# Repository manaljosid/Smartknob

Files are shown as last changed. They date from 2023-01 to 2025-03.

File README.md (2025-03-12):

# Smartknob
A smartknob clone based on the [original project](https://github.com/scottbez1/smartknob) from Scott Bezek.

A couple changes are implemented including:
- Change of microcontroller from ESP32 to RP2040
- Change of load cell setup from dedicated loadcells to resistors
- Change of HX711 load cell amplifier to MCP3564R 24-bit ADC
- Change of RGB LEDs to ones from Adafruit

The project uses Altium Designer for schematic and PCB design, Autodesk Fusion 360 for mechanical design and the Pico SDK for software development.

## Heads-up!
No guarantee is made that anything in this repository will work. Currently all changes are committed directly to the main branch and as such the main branch can contain bugs or have changes that have yet to be completed.

## Installation
### Schematic and PCB design
The designs are made with the latest version of Altium Designer and as such the software along with a valid license is required.

In addition to Altium Designer the component library used for all of my projects needs to be installed. It can be found on this [github repository](https://github.com/manaljosid/Moonlight_Library).

### Mechanical design
The mechanical design is not available at the moment other than the STL files used for 3D printing.

### Software development
In addition to pulling this repository you need to fetch all required submodules. Those include the actual pico-sdk and its submodules. Make sure the submodules are all installed, if the submodules of the pico-sdk are not installed then no USB function other than the boot ROM will work.

Due to issues in the release of the pico-sdk being used for this code (mainly that the clock configuration is hard coded) a development branch is used.

## Things to watch out for
The MCP3564R *NEEDS* a pull-up on the IRQ line when it is in high-z mode. It can be weak - about 100 kOhm will do but if it is not there the ADCDATA register will never contain any data. In this case it is solved using a pull-up on the RP2040s GPIO pin that's connected to the IRQ line.

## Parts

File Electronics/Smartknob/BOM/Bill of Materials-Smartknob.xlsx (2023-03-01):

Description | Supplier | Designator | Supplier Part No | Quantity | Fitted | Generic | Value
General purpose ceramic capacitor | Digi-Key | C100 | 445-5691-1-ND | 1 | Fitted | Generic | 2.2uF
General purpose ceramic capacitor | Digi-Key | C101, C208, C209, C504, C505 | 445-174215-1-ND | 5 | Fitted | Generic | 1uF
General purpose ceramic capacitor | Digi-Key | C102, C302, C303 | 445-16110-1-ND | 3 | Fitted | Generic | 10uF
General purpose ceramic capacitor | Digi-Key | C200, C201, C202, C203, C204, C205, C206, C207, C210, C211, C300, C301, C304, C305, C400, C500, C501, C502, C503, C600, C601, C602, C603, C604, C605, C606, C607, C608 | 445-5666-1-ND | 28 | Fitted | Generic | 100nF
General purpose ceramic capacitor | Digi-Key | C212, C213 | 445-5634-1-ND | 2 | Fitted | Generic | 33pF
Side mounted RGB neopixel | Digi-Key | D600, D601, D602, D603, D604, D605, D606, D607 | 1528-4691-ND | 8 | Fitted | Non Generic | RGB
PTC resettable SMD fuse | Digi-Key | F200 | MF-PSMF050X-2CT-ND | 1 | Fitted | Generic | 500 mA
Ferrite bead | Digi-Key | FB500 | 587-FBTH1608HL221-TCT-ND | 1 | Fitted | Generic
3 pin horizontal picoblade connector | Digi-Key | J100 | WM7621CT-ND | 1 | Fitted | Non Generic
2mm pitch solder pads, M1.6 Hole, Unplated, M2 Hole, Unplated, SMD Testpoint, pad style |  | J101, M100, M101, M102, M103, M104, M105, M106, M107, M108, TP200 |  | 11 | Fitted | Generic
3 pin vertical 2.54 mm header | Digi-Key | J102 | 732-5316-ND | 1 | Fitted | Generic
USB 2.0 Type C connector | Digi-Key | J200 | 670-DX07S016JA1R1500CT-ND | 1 | Fitted | Non Generic
General purpose automotive thick film resistor | Digi-Key | R100, R101 | 541-2.2KGCT-ND | 2 | Not Fitted | Generic | 2K2
General purpose automotive thick film resistor | Digi-Key | R200, R205 | 541-1.0KGCT-ND | 2 | Fitted | Generic | 1K
General purpose automotive thick film resistor | Digi-Key | R201, R204 | 541-5.10KHCT-ND | 2 | Fitted | Generic | 5K1
General purpose automotive thick film resistor | Digi-Key | R202, R203 | 541-27GCT-ND | 2 | Fitted | Generic | 27R
General purpose automotive thick film resistor | Digi-Key | R206, R300, R301, R302, R303, R304, R305 | 541-10KGCT-ND | 7 | Fitted | Generic | 10K
General purpose automotive thick film resistor | Digi-Key | R400, R401 | 541-2.2KGCT-ND | 2 | Fitted | Generic | 2K2
General purpose automotive thick film resistor | Digi-Key | R500, R501 | 541-10GCT-ND | 2 | Fitted | Generic | 10R
General purpose automotive thick film resistor | Digi-Key | R502, R503, R506, R507 | 541-330XCT-ND | 4 | Fitted | Generic | 330R
General purpose automotive thick film resistor | Digi-Key | R504, R505 | 541-100GCT-ND | 2 | Fitted | Generic | 100R
General purpose automotive thick film resistor | Digi-Key | R508 | 541-0.0GCT-ND | 1 | Fitted | Generic | 0R
SPST Tactile Switch 4.2x3.2 mm | Digi-Key | SW200, SW201 | 732-13663-1-ND | 2 | Fitted | Non Generic
SMD Testpoint, loop style | Digi-Key | TP100, TP101, TP102, TP103, TP201, TP202 | 36-5019CT-ND | 6 | Fitted | Generic
3.3V 700mA LDO linear regulator | Digi-Key | U100 | 893-1143-1-ND | 1 | Fitted | Non Generic
128 Mbit SPI/QSPI Flash memory | Digi-Key | U200 | W25Q128JVSIQ-ND | 1 | Fitted | Non Generic
Dual Core 133 MHz ARM-M0 Microcontroller | Digi-Key | U201 | 2648-SC0908(7)CT-ND | 1 | Fitted | Non Generic
2-11V 2A 3-phase BLDC motor driver | Digi-Key | U300 | 1460-TMC6300-LA-TCT-ND | 1 | Fitted | Non Generic
Hall effect absolute magnetic encoder | LCSC | U400 | C2856764 | 1 | Fitted | Non Generic
Low-noise 24-bit Delta-Sigma ADC, 2/4/8 ch single ended, 1/2/4 ch differential | Digi-Key | U500 | 150-MCP3564RT-E/STCT-ND | 1 | Fitted | Non Generic
Single Buffer CMOS Level Shifter | Digi-Key | U600 | 296-37176-1-ND | 1 | Fitted | Generic
12 MHz 10ppm crystal oscillator | Digi-Key | X200 | XC1810CT-ND | 1 | Fitted | Non Generic | 12 MHz

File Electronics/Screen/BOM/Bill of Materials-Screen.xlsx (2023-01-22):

Description | Supplier | Designator | Supplier Part No | Quantity | Fitted | Generic | Value
General purpose ceramic capacitor | Digi-Key | C1 | 445-5666-1-ND | 1 | Fitted | Generic | 100nF
General purpose ceramic capacitor | Digi-Key | C2, C3 | 445-16110-1-ND | 2 | Fitted | Generic | 10uF
2mm pitch solder pads, M1.6 Hole, Unplated |  | J1, J2, M1 |  | 3 | Fitted | Generic
General purpose N-Channel MOSFET in SOT23 packagge | Digi-Key | Q1 | BSS138CT-ND | 1 | Fitted | Generic | NMOS
General purpose automotive thick film resistor | Digi-Key | R1 | 541-22GCT-ND | 1 | Fitted | Generic | 22R
General purpose automotive thick film resistor | Digi-Key | R2 | 541-10KGCT-ND | 1 | Fitted | Generic | 10K
General purpose automotive thick film resistor | Digi-Key | R3 | 541-1.0MGCT-ND | 1 | Fitted | Generic | 1M
240x240 px round IPS display | N/A | U1 | N/A | 1 | Fitted | Non Generic | Display

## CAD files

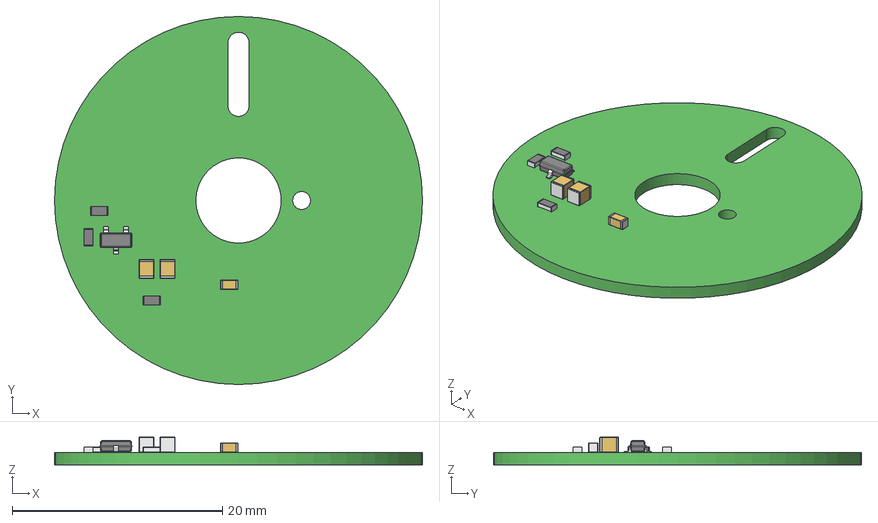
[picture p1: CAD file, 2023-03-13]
Electronics/Screen/Screen.step
35.0 x 35.0 x 2.65 mm
Mid_Body x 3
Mark x 3
Leader x 3

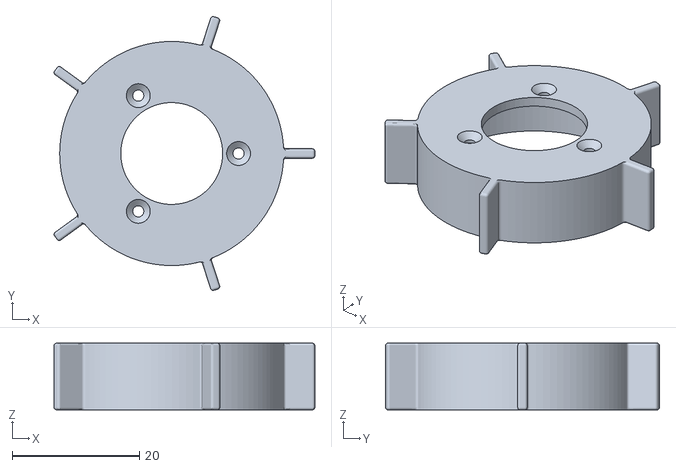
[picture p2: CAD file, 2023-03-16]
Mechanical/Exports/RotorSpacer.stl
41.0 x 43.0 x 10.5

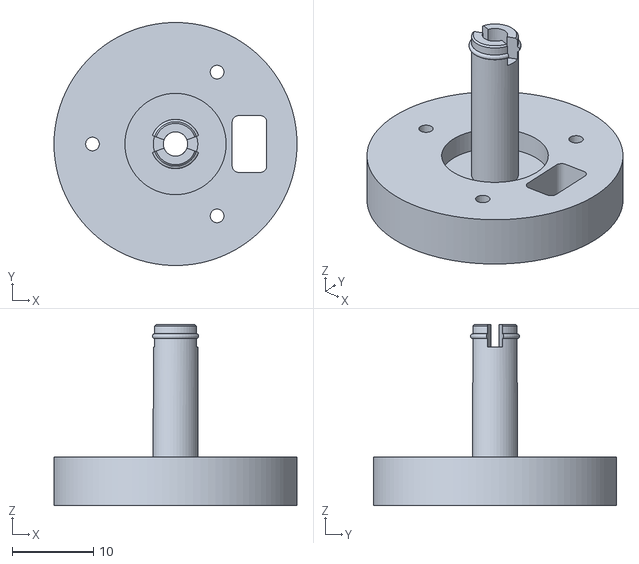
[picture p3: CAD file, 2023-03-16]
Mechanical/Exports/BaseMount.stl
30.0 x 30.0 x 22.3

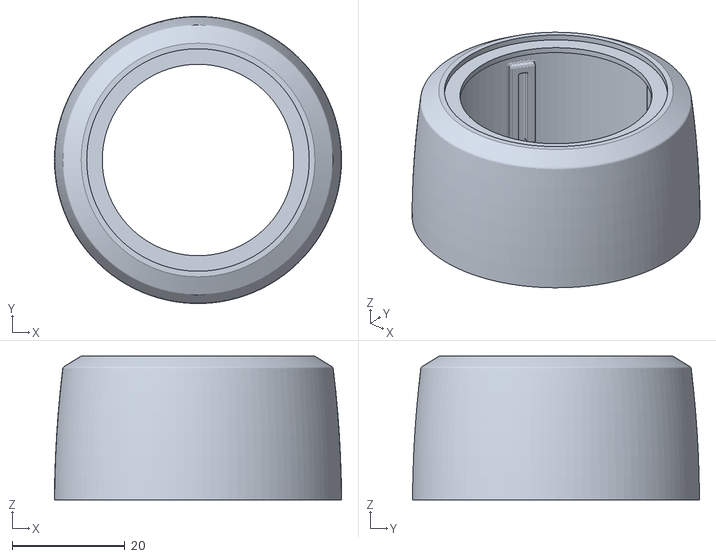
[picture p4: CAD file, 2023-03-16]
Mechanical/Exports/Knob.stl
51.0 x 51.0 x 25.6

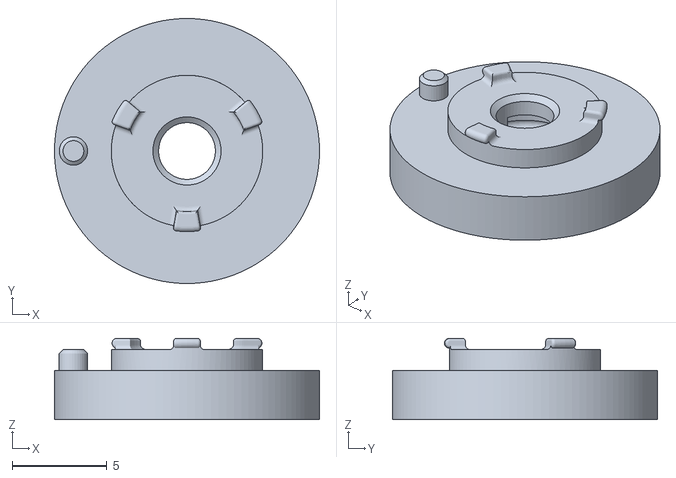
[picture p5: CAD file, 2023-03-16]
Mechanical/Exports/ScreenPlatform.stl
14.0 x 14.0 x 4.30

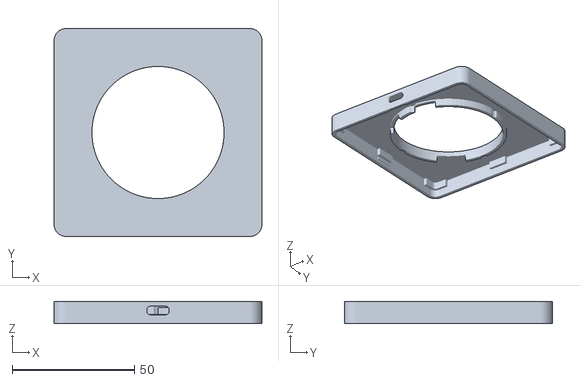
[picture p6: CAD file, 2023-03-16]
Mechanical/Exports/Enclosure.stl
85.0 x 85.0 x 9.00

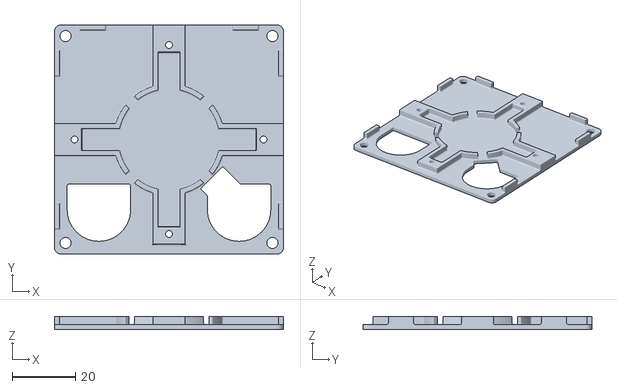
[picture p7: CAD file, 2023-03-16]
Mechanical/Exports/Baseplate.stl
72.2 x 72.2 x 4.00

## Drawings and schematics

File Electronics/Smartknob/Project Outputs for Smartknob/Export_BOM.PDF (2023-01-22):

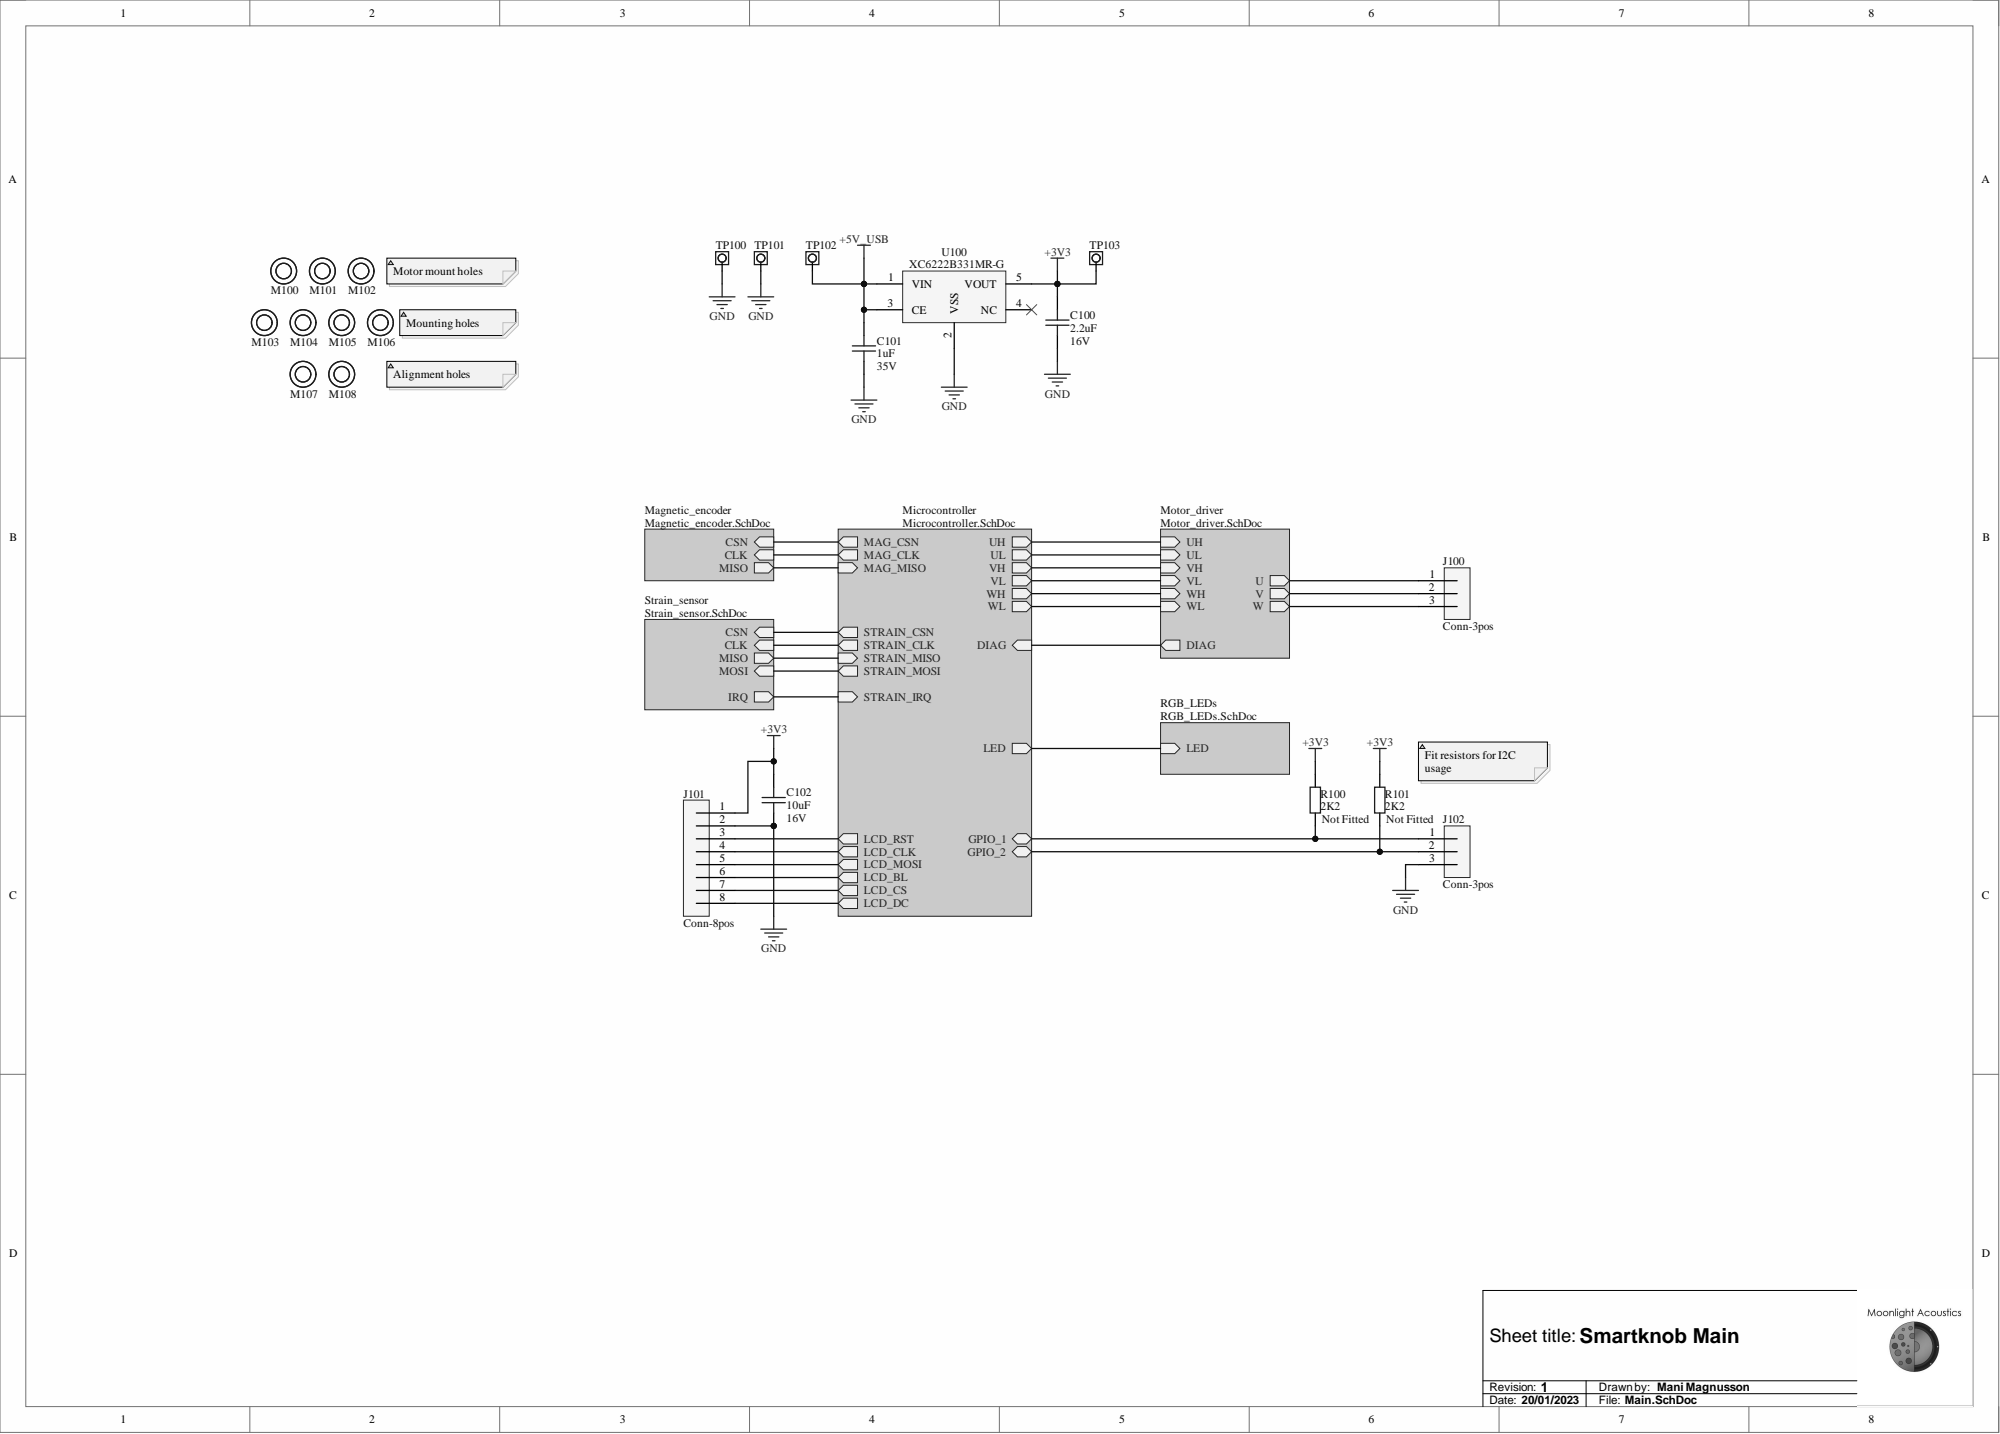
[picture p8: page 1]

Drawn by: Mani Magnusson
File: Main.SchDoc

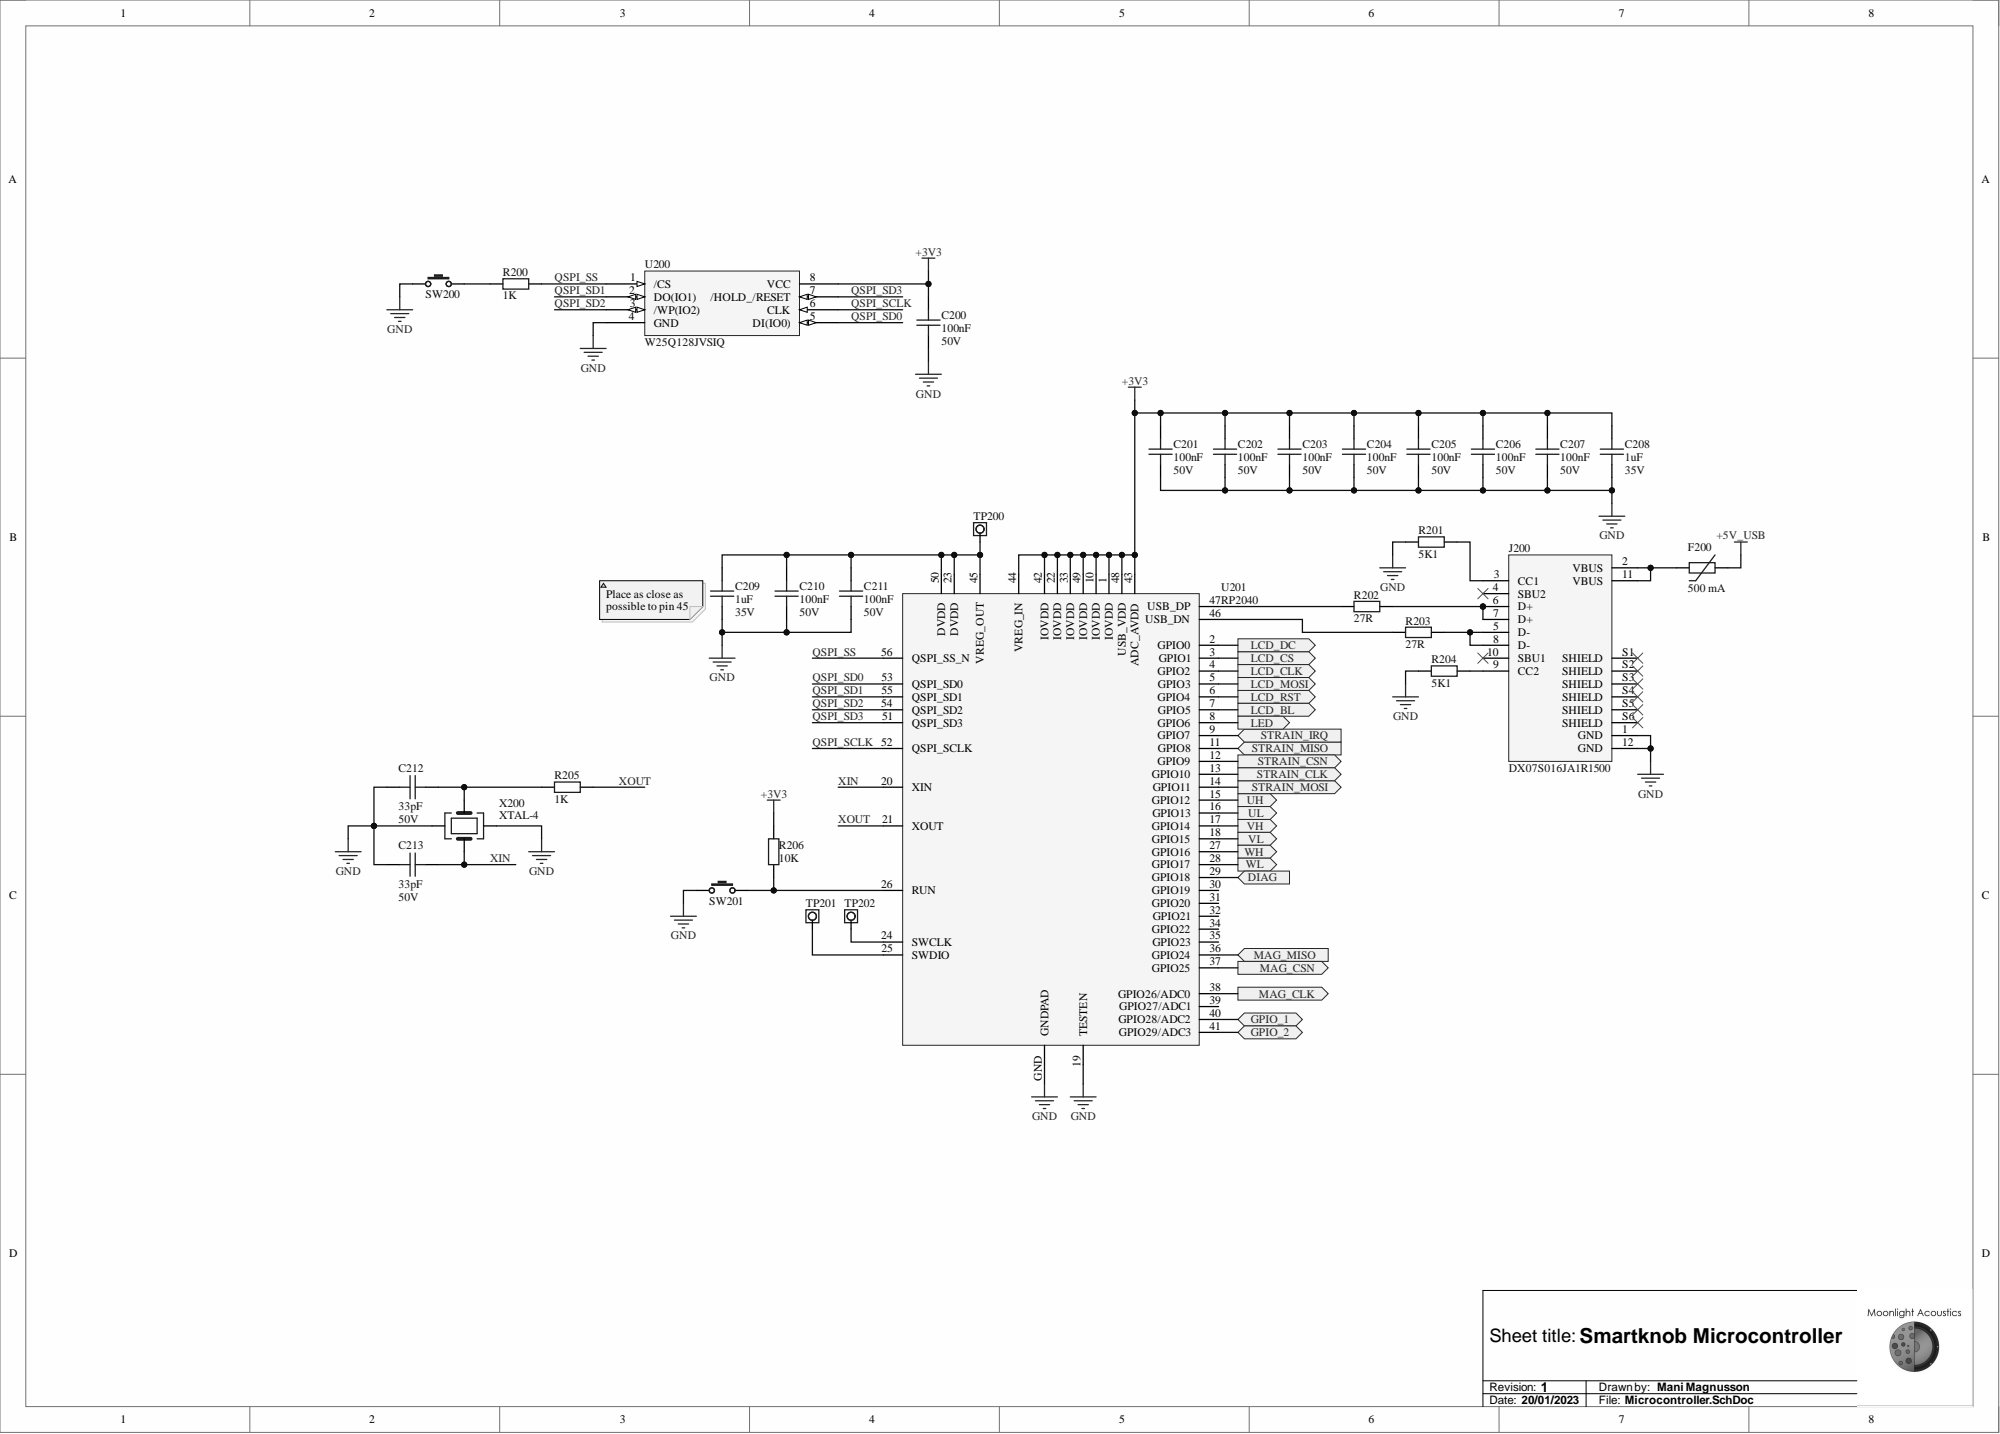
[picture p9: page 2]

Place as close as
possible to pin 45

QSPI_SS | | | D- 8

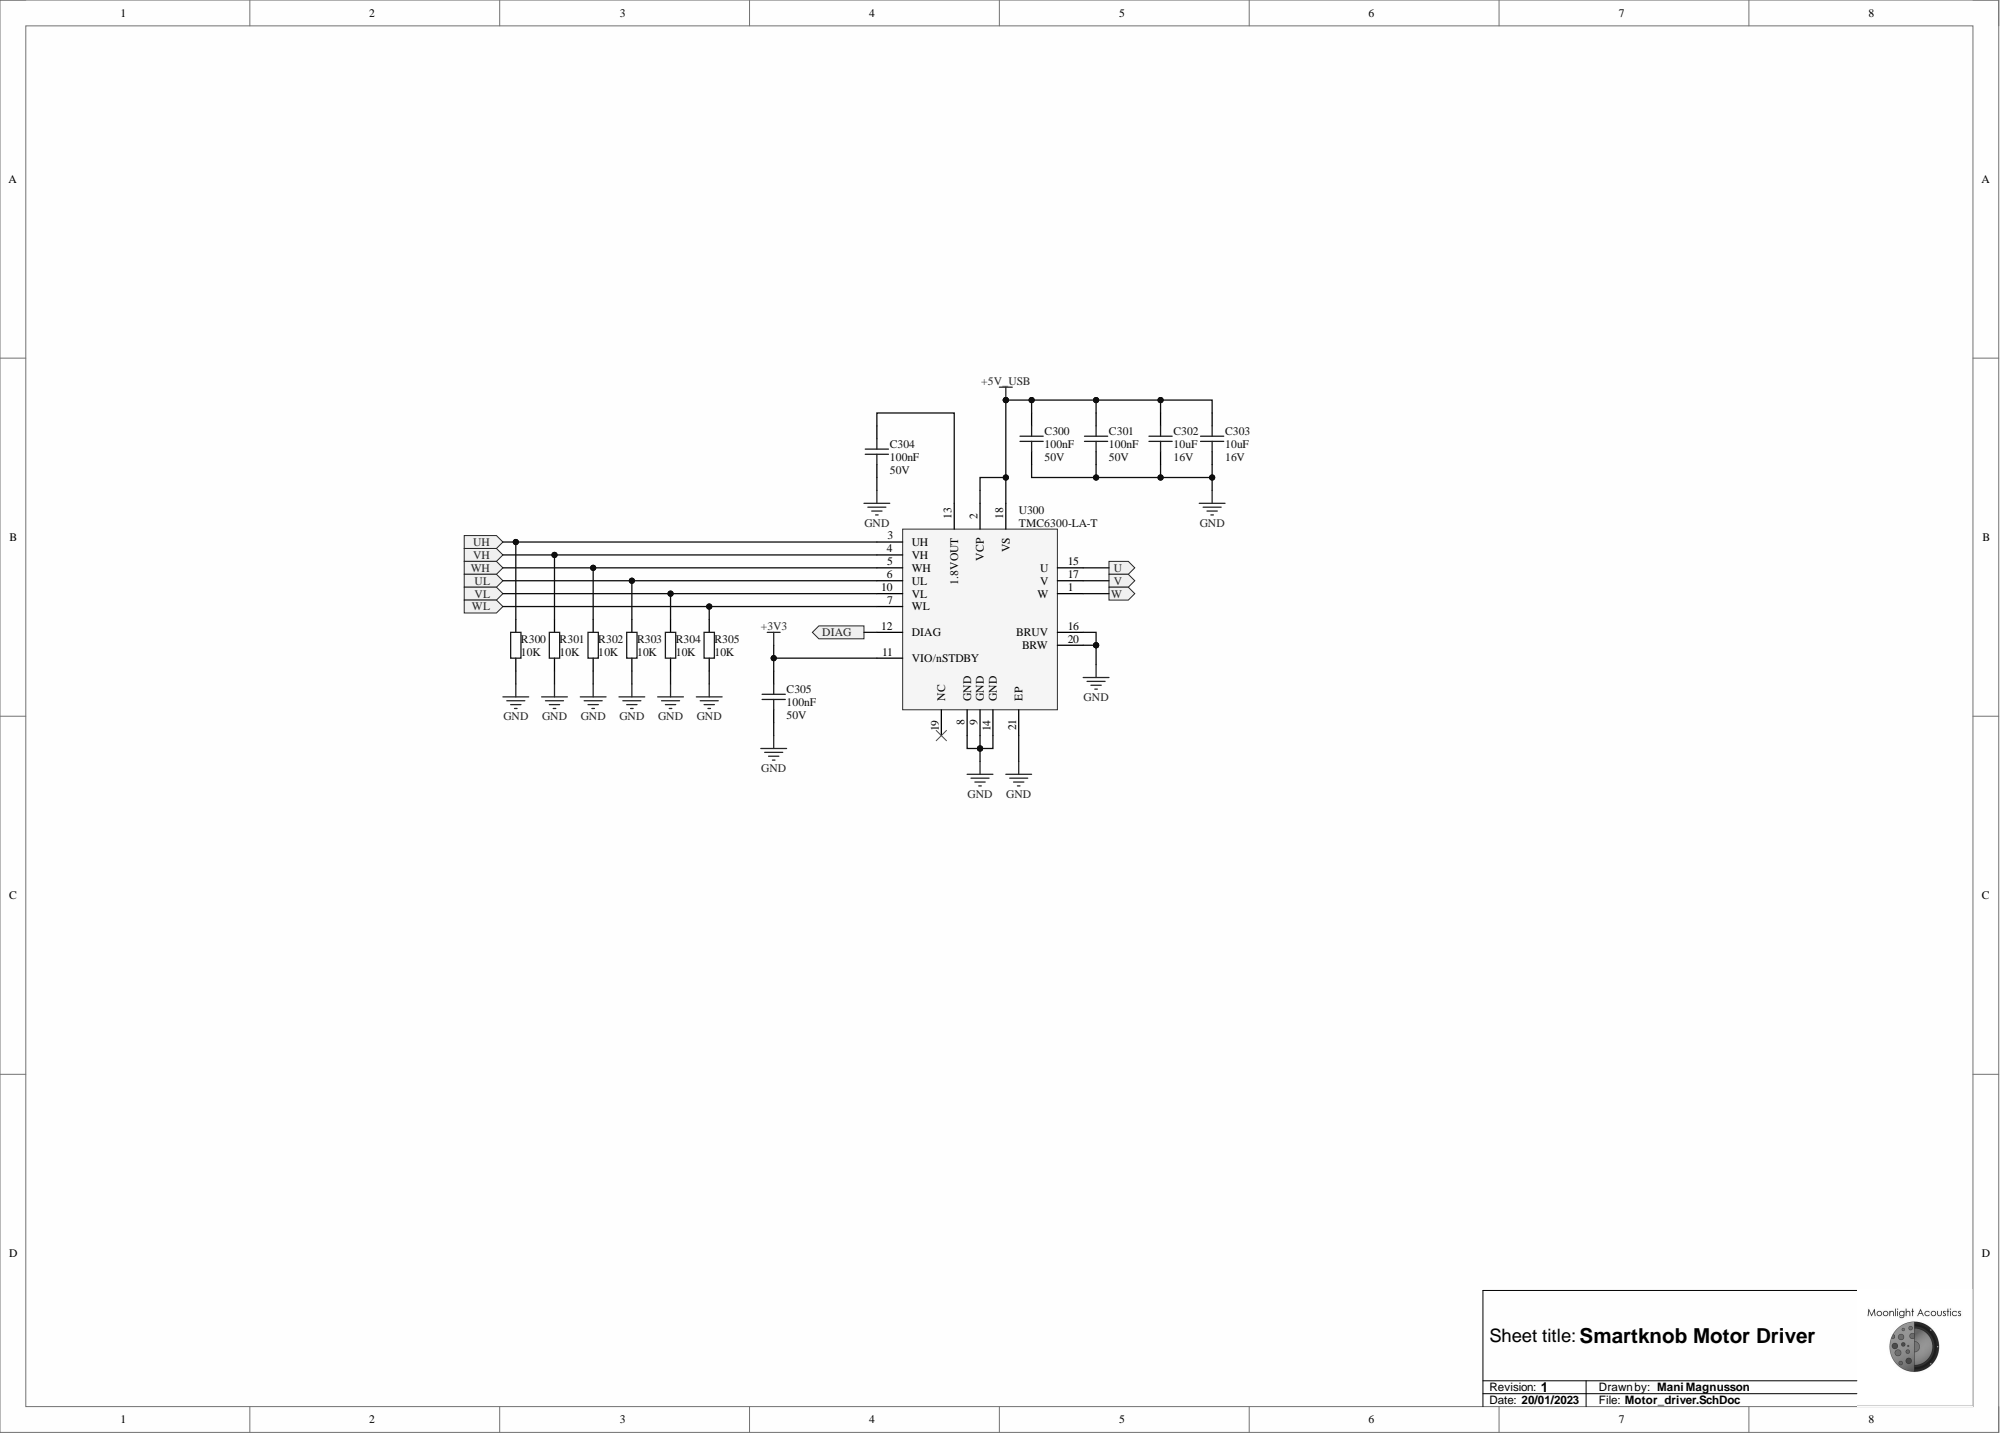
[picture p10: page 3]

1 0

Sheet title: Date: Revision:

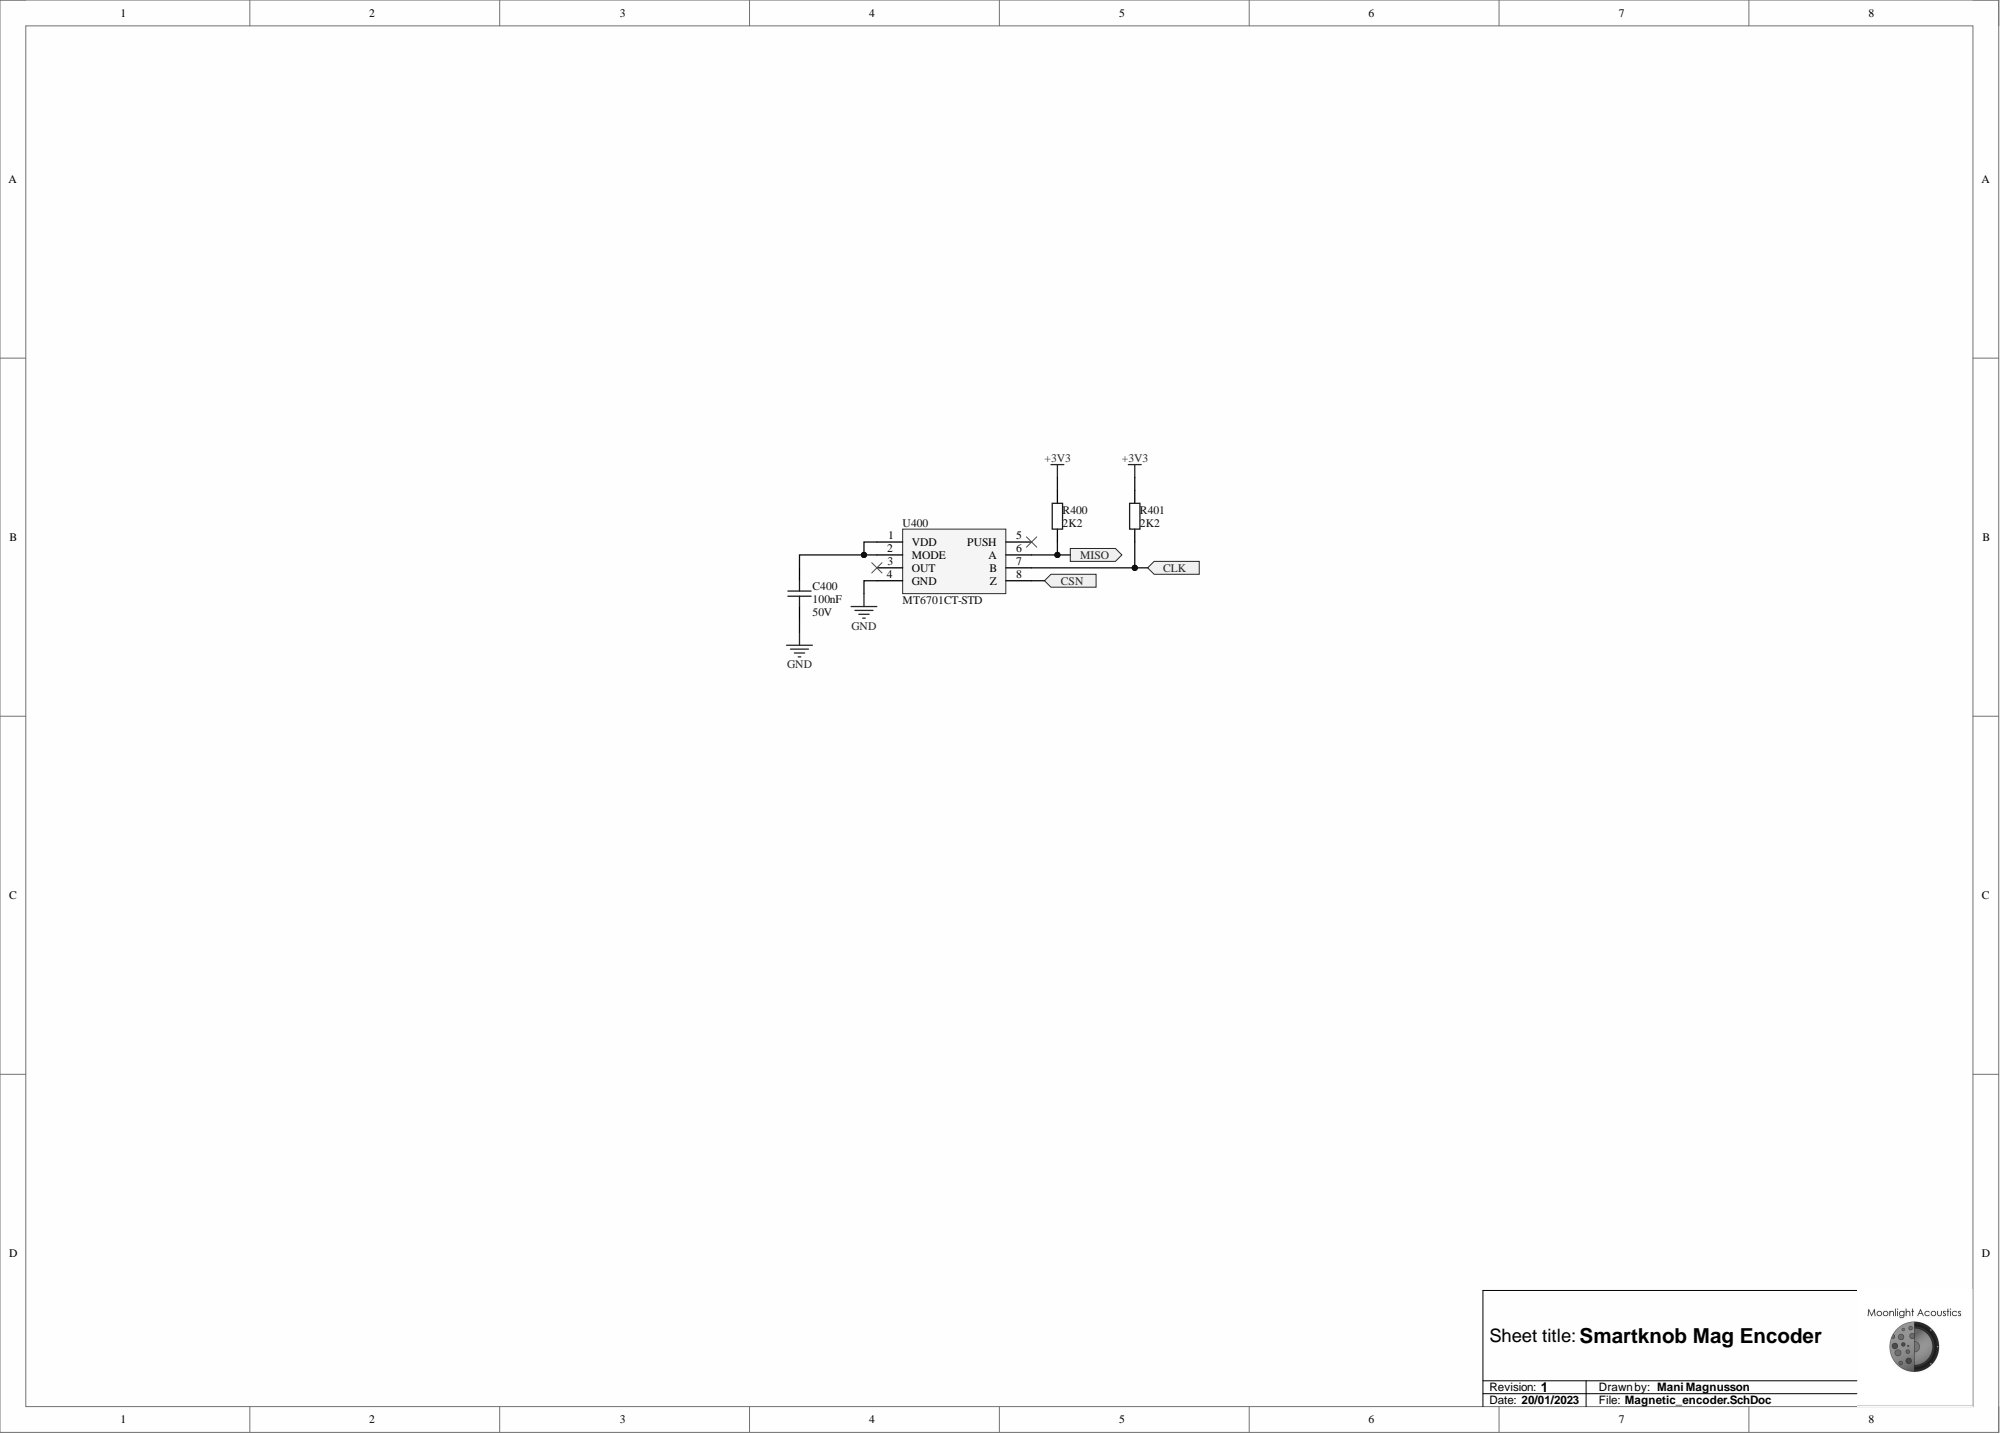
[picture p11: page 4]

Sheet title: Date: Revision:

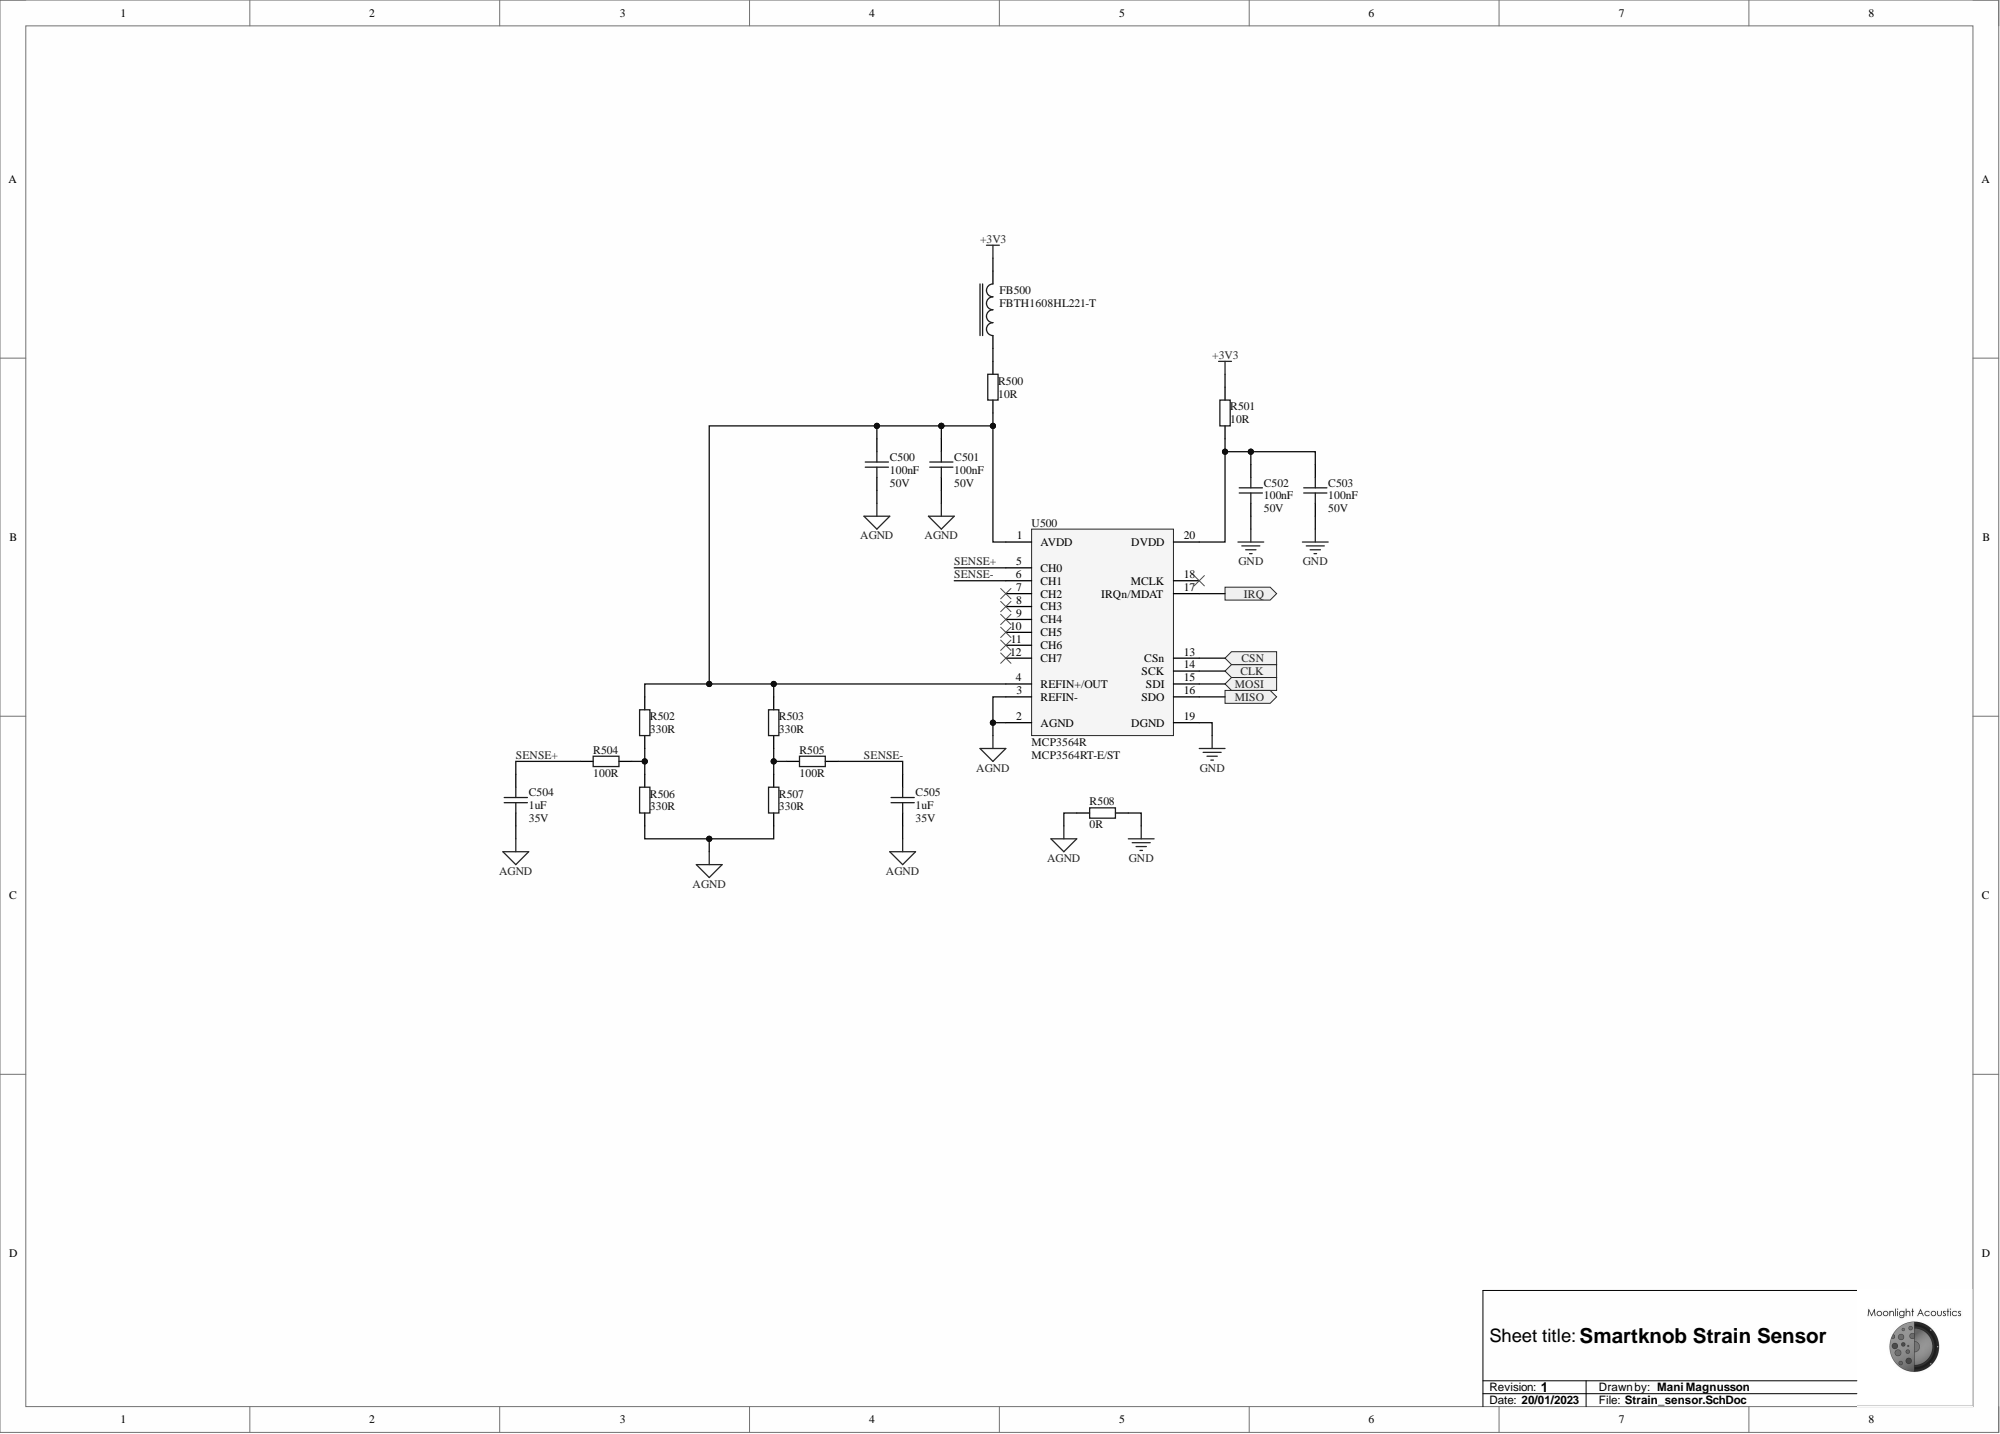
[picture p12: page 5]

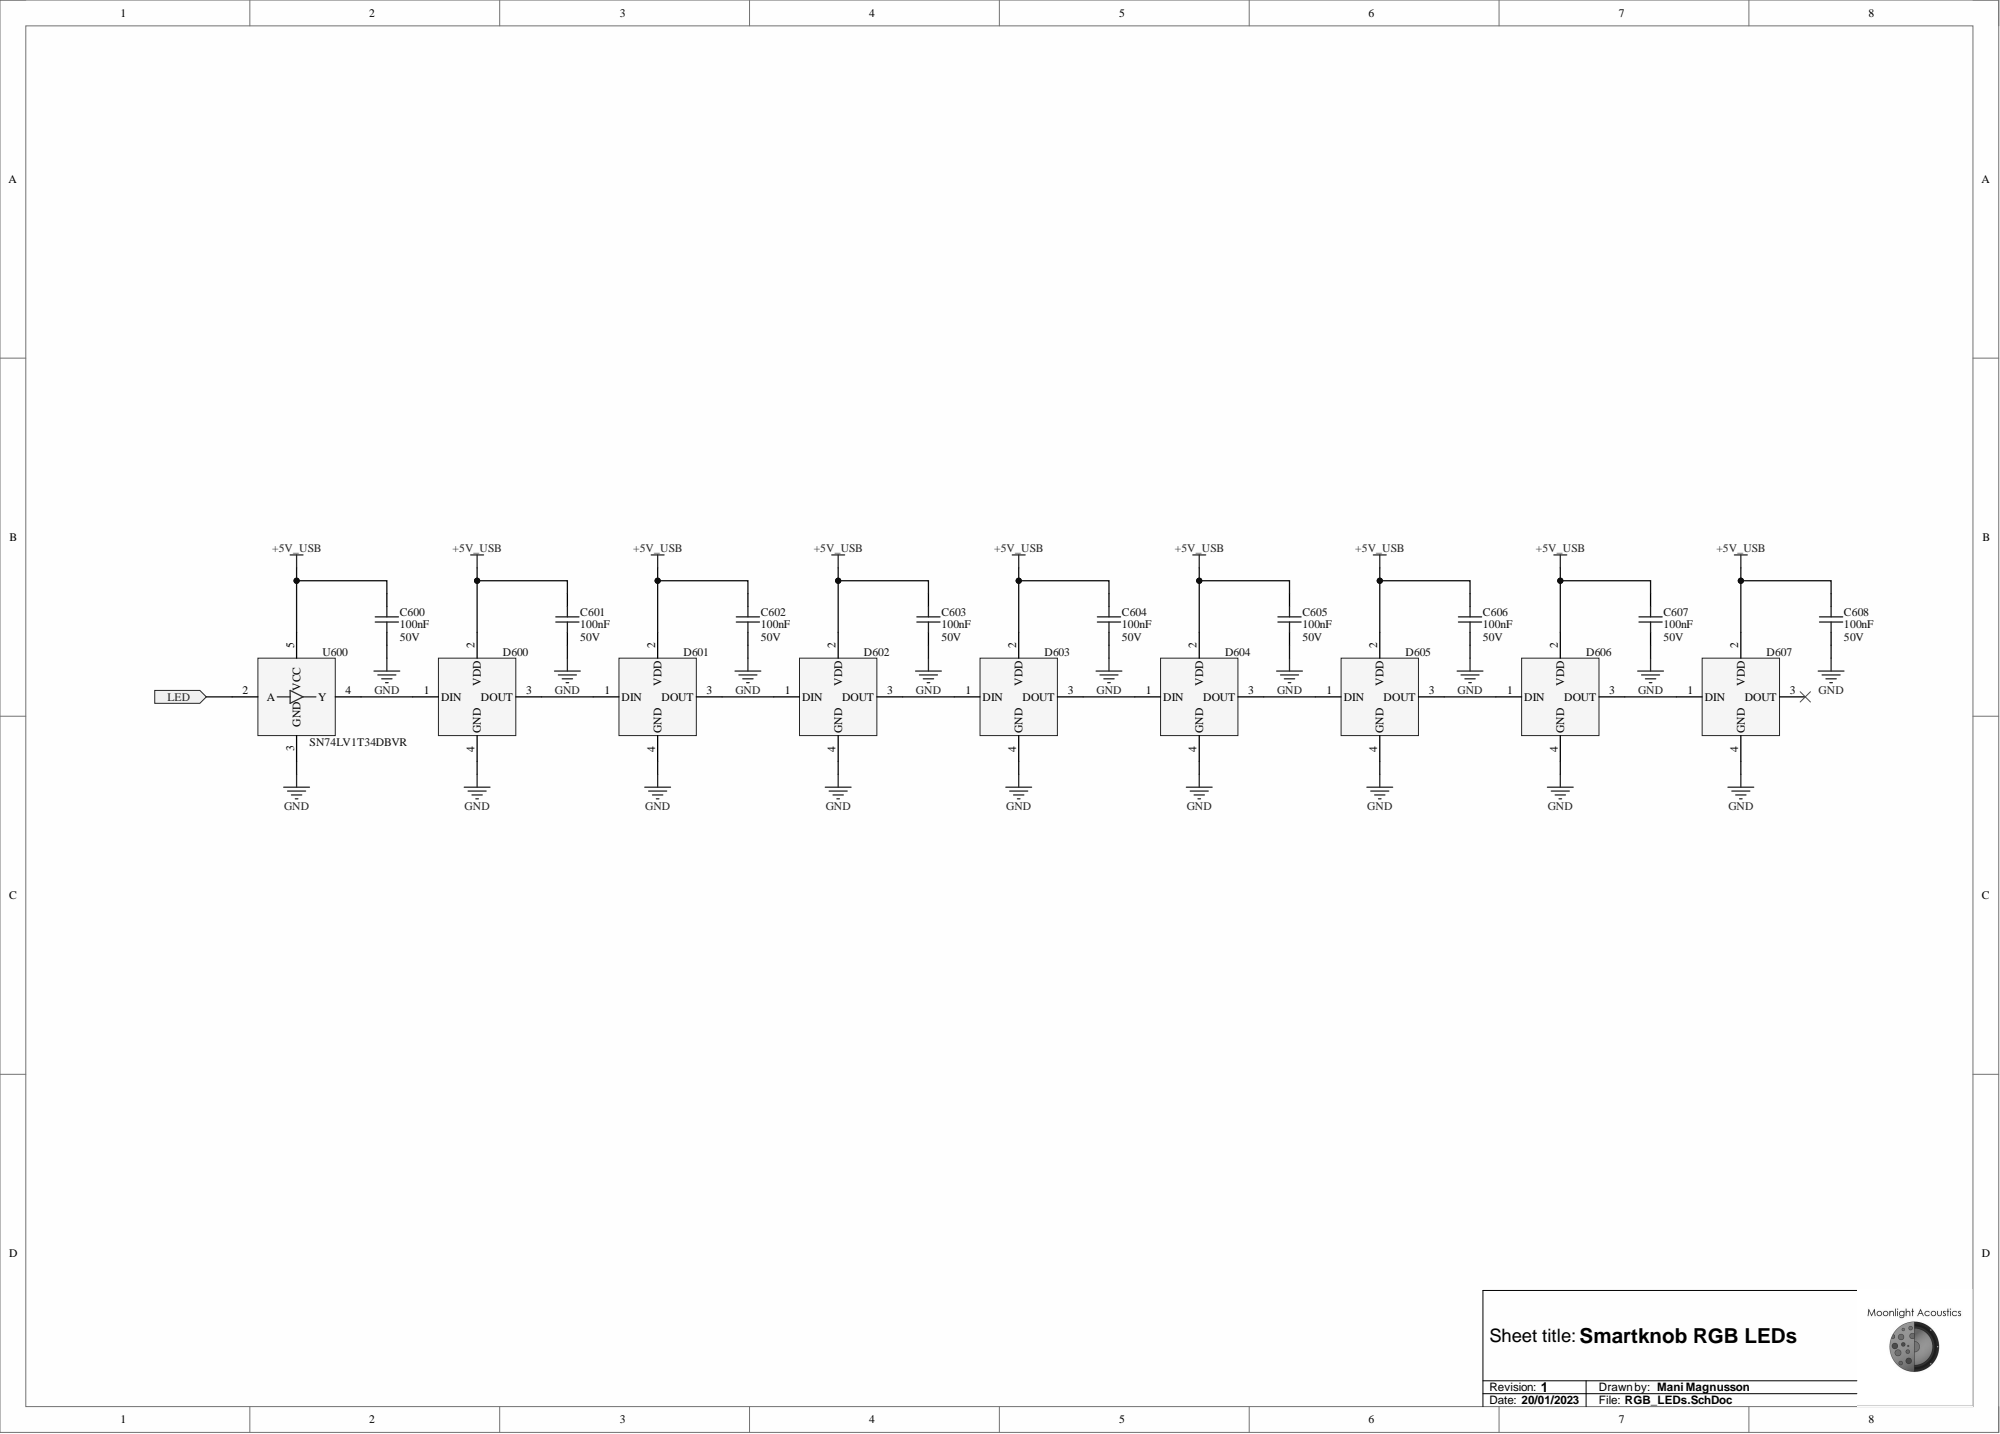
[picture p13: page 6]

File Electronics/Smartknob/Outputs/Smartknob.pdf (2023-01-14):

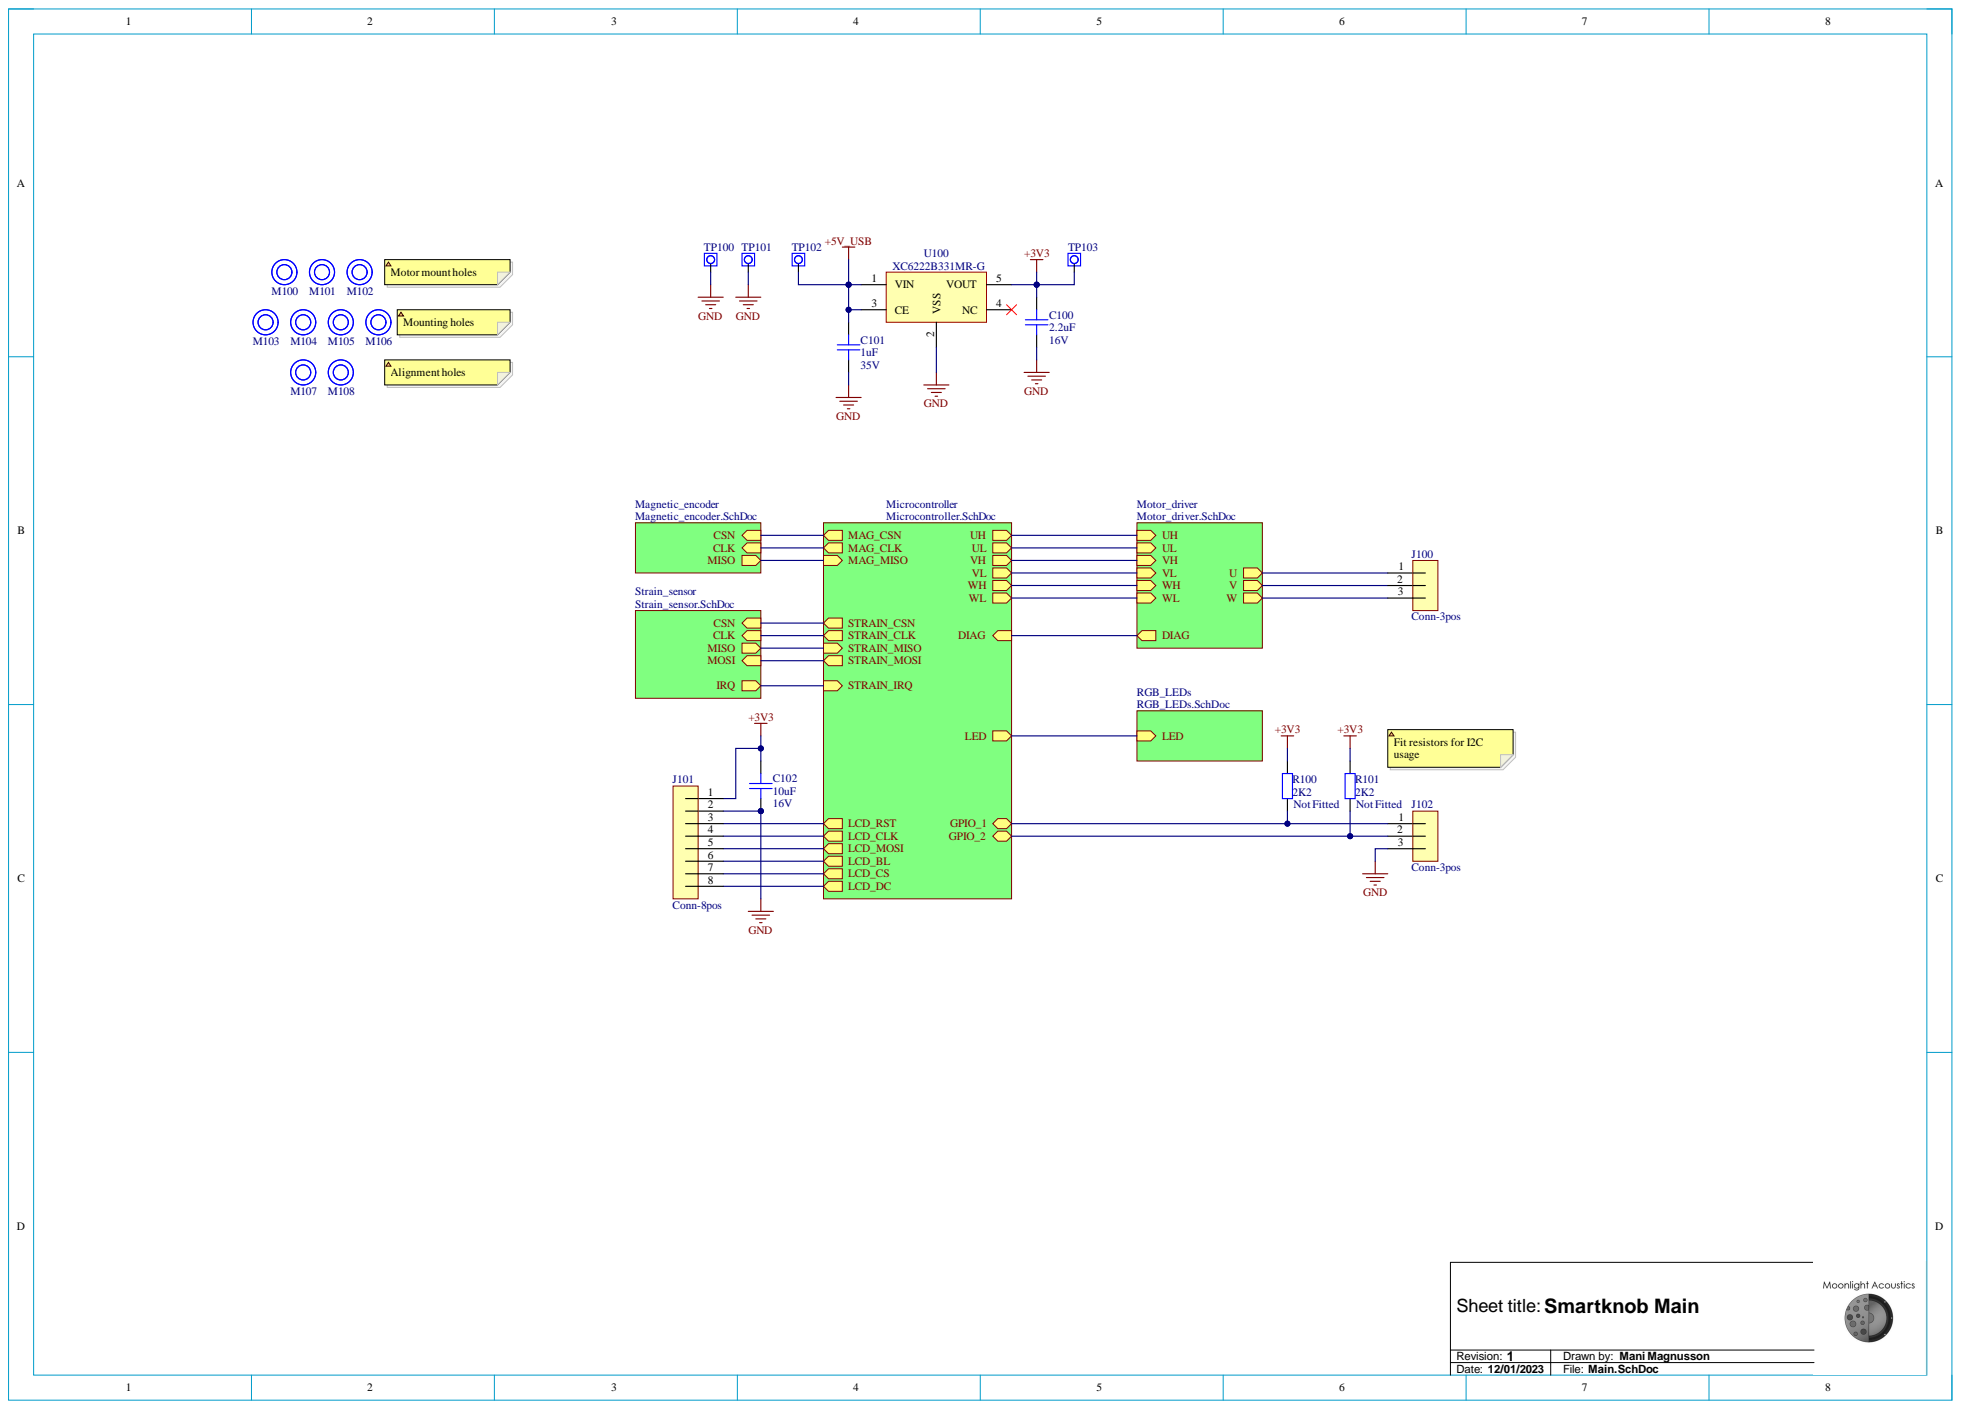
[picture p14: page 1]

Drawn by: Mani Magnusson
File: Main.SchDoc

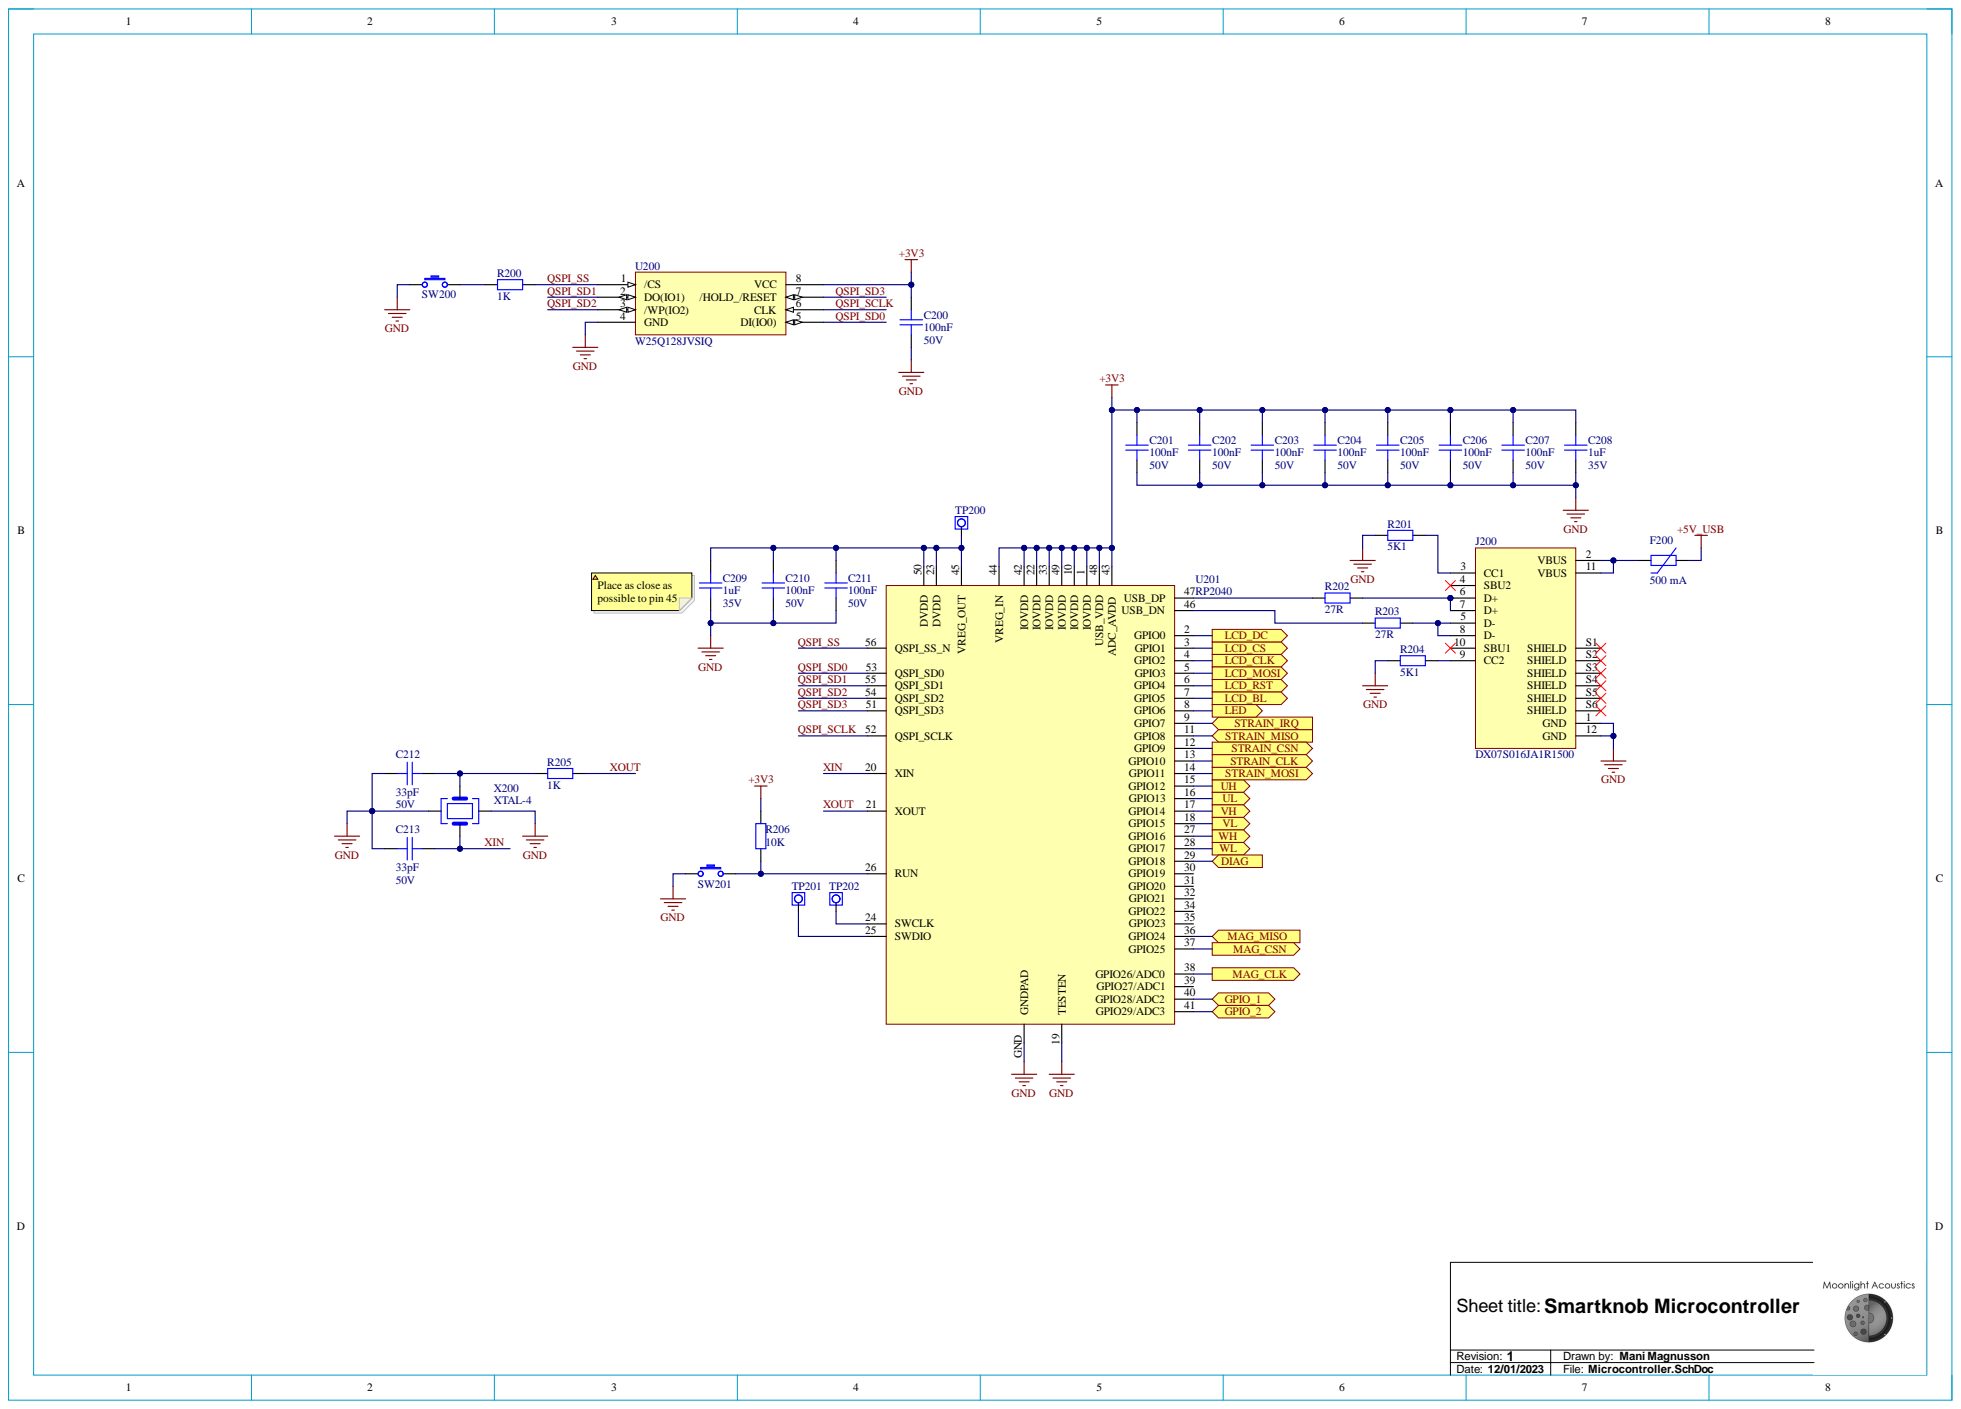
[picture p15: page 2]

Place as close as
possible to pin 45

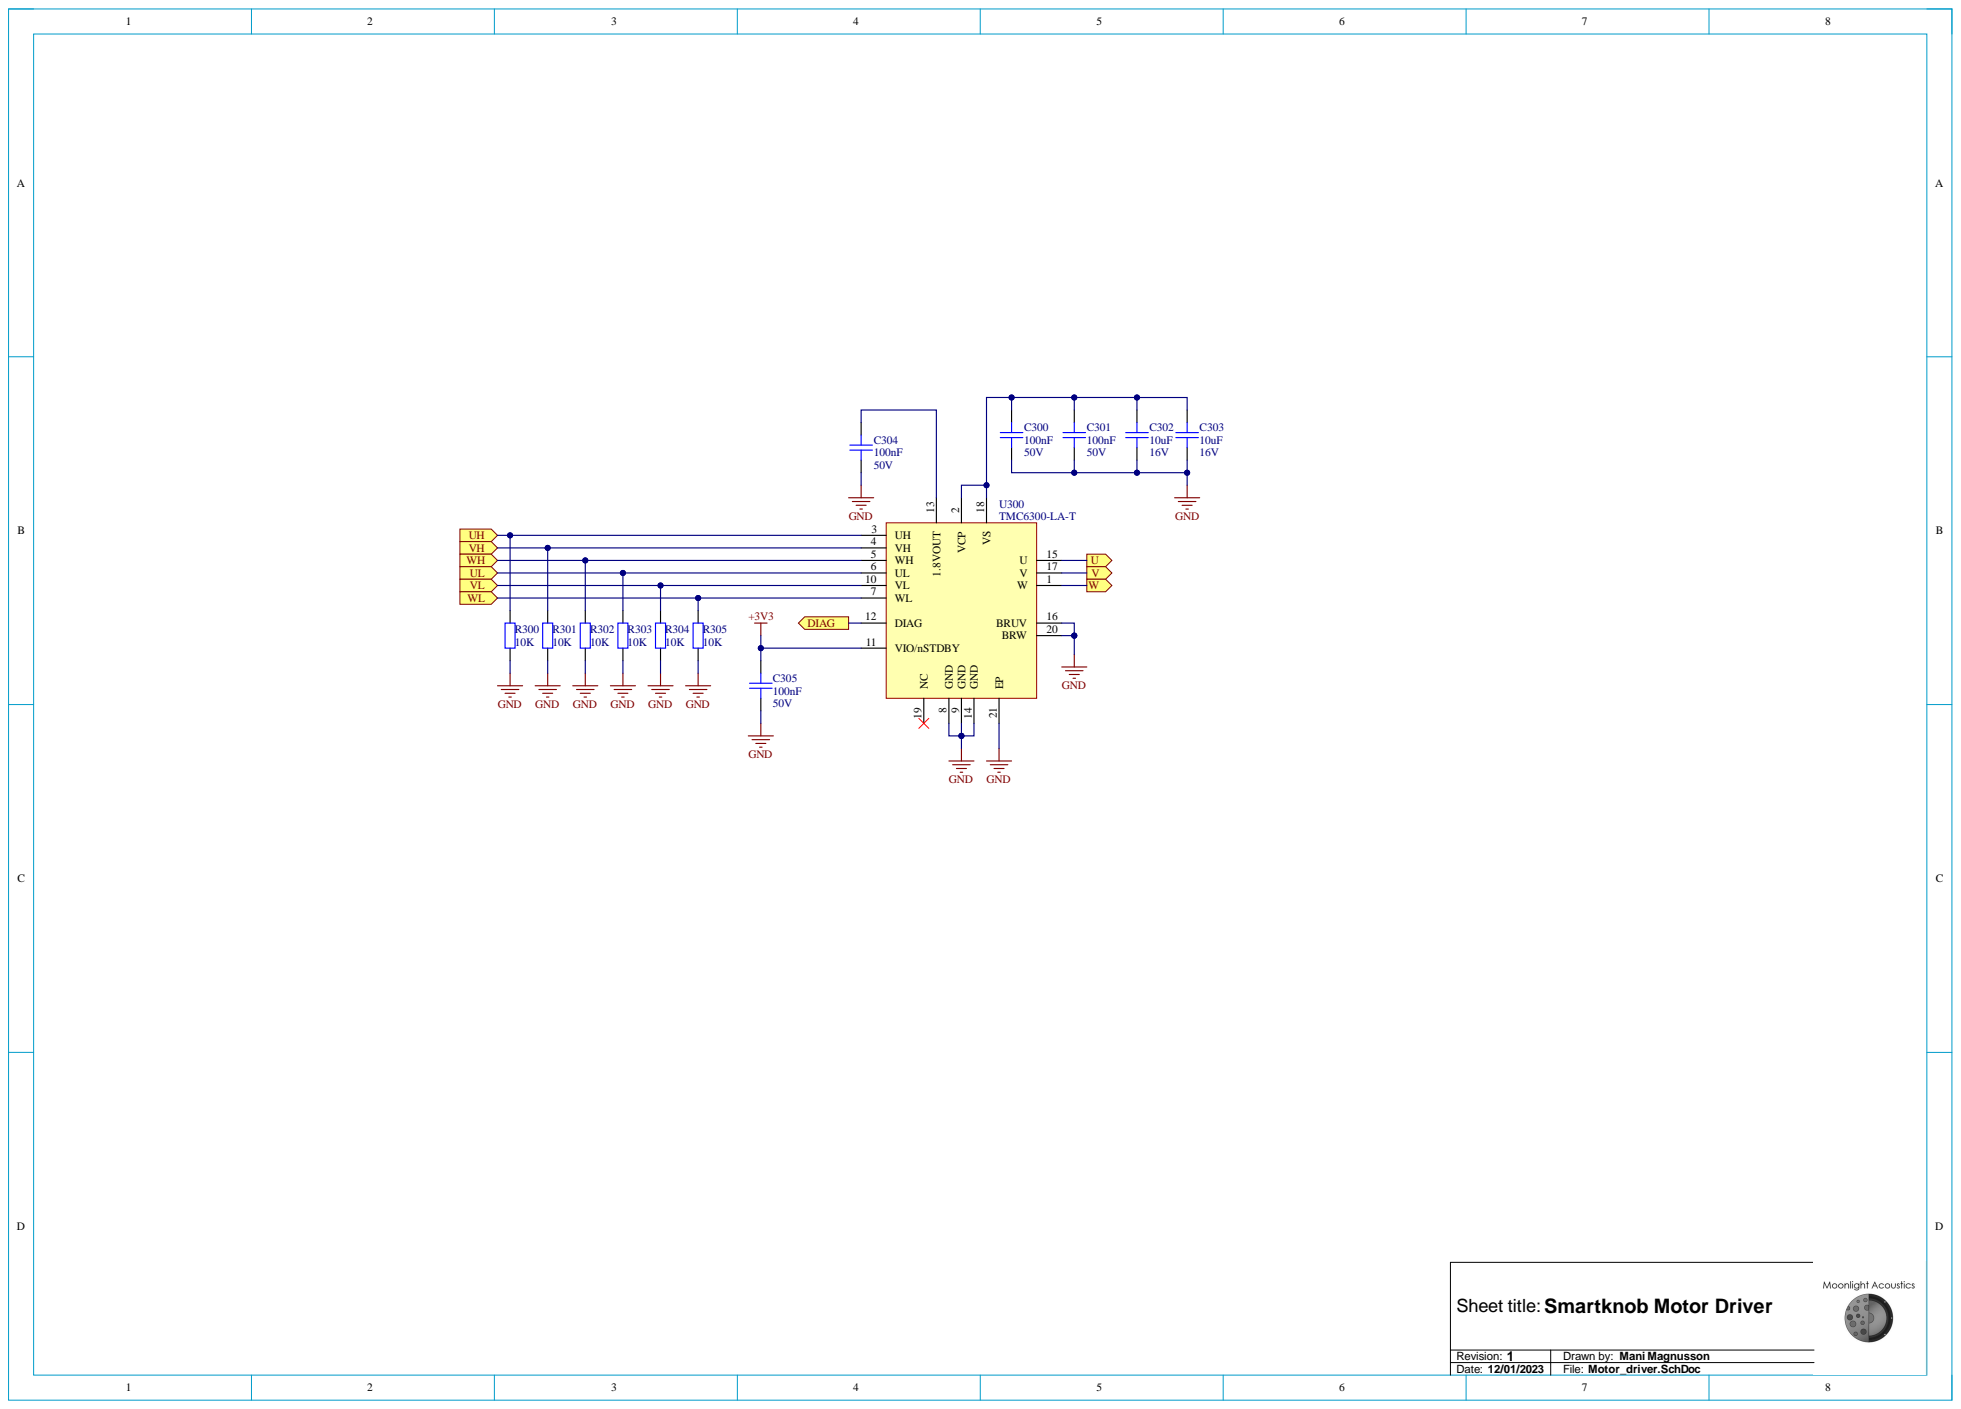
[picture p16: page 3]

VH 4
WH 5
UL 6
VL 10
WL 7

+3V3 | DIAG 12 VIO/nSTDBY 11

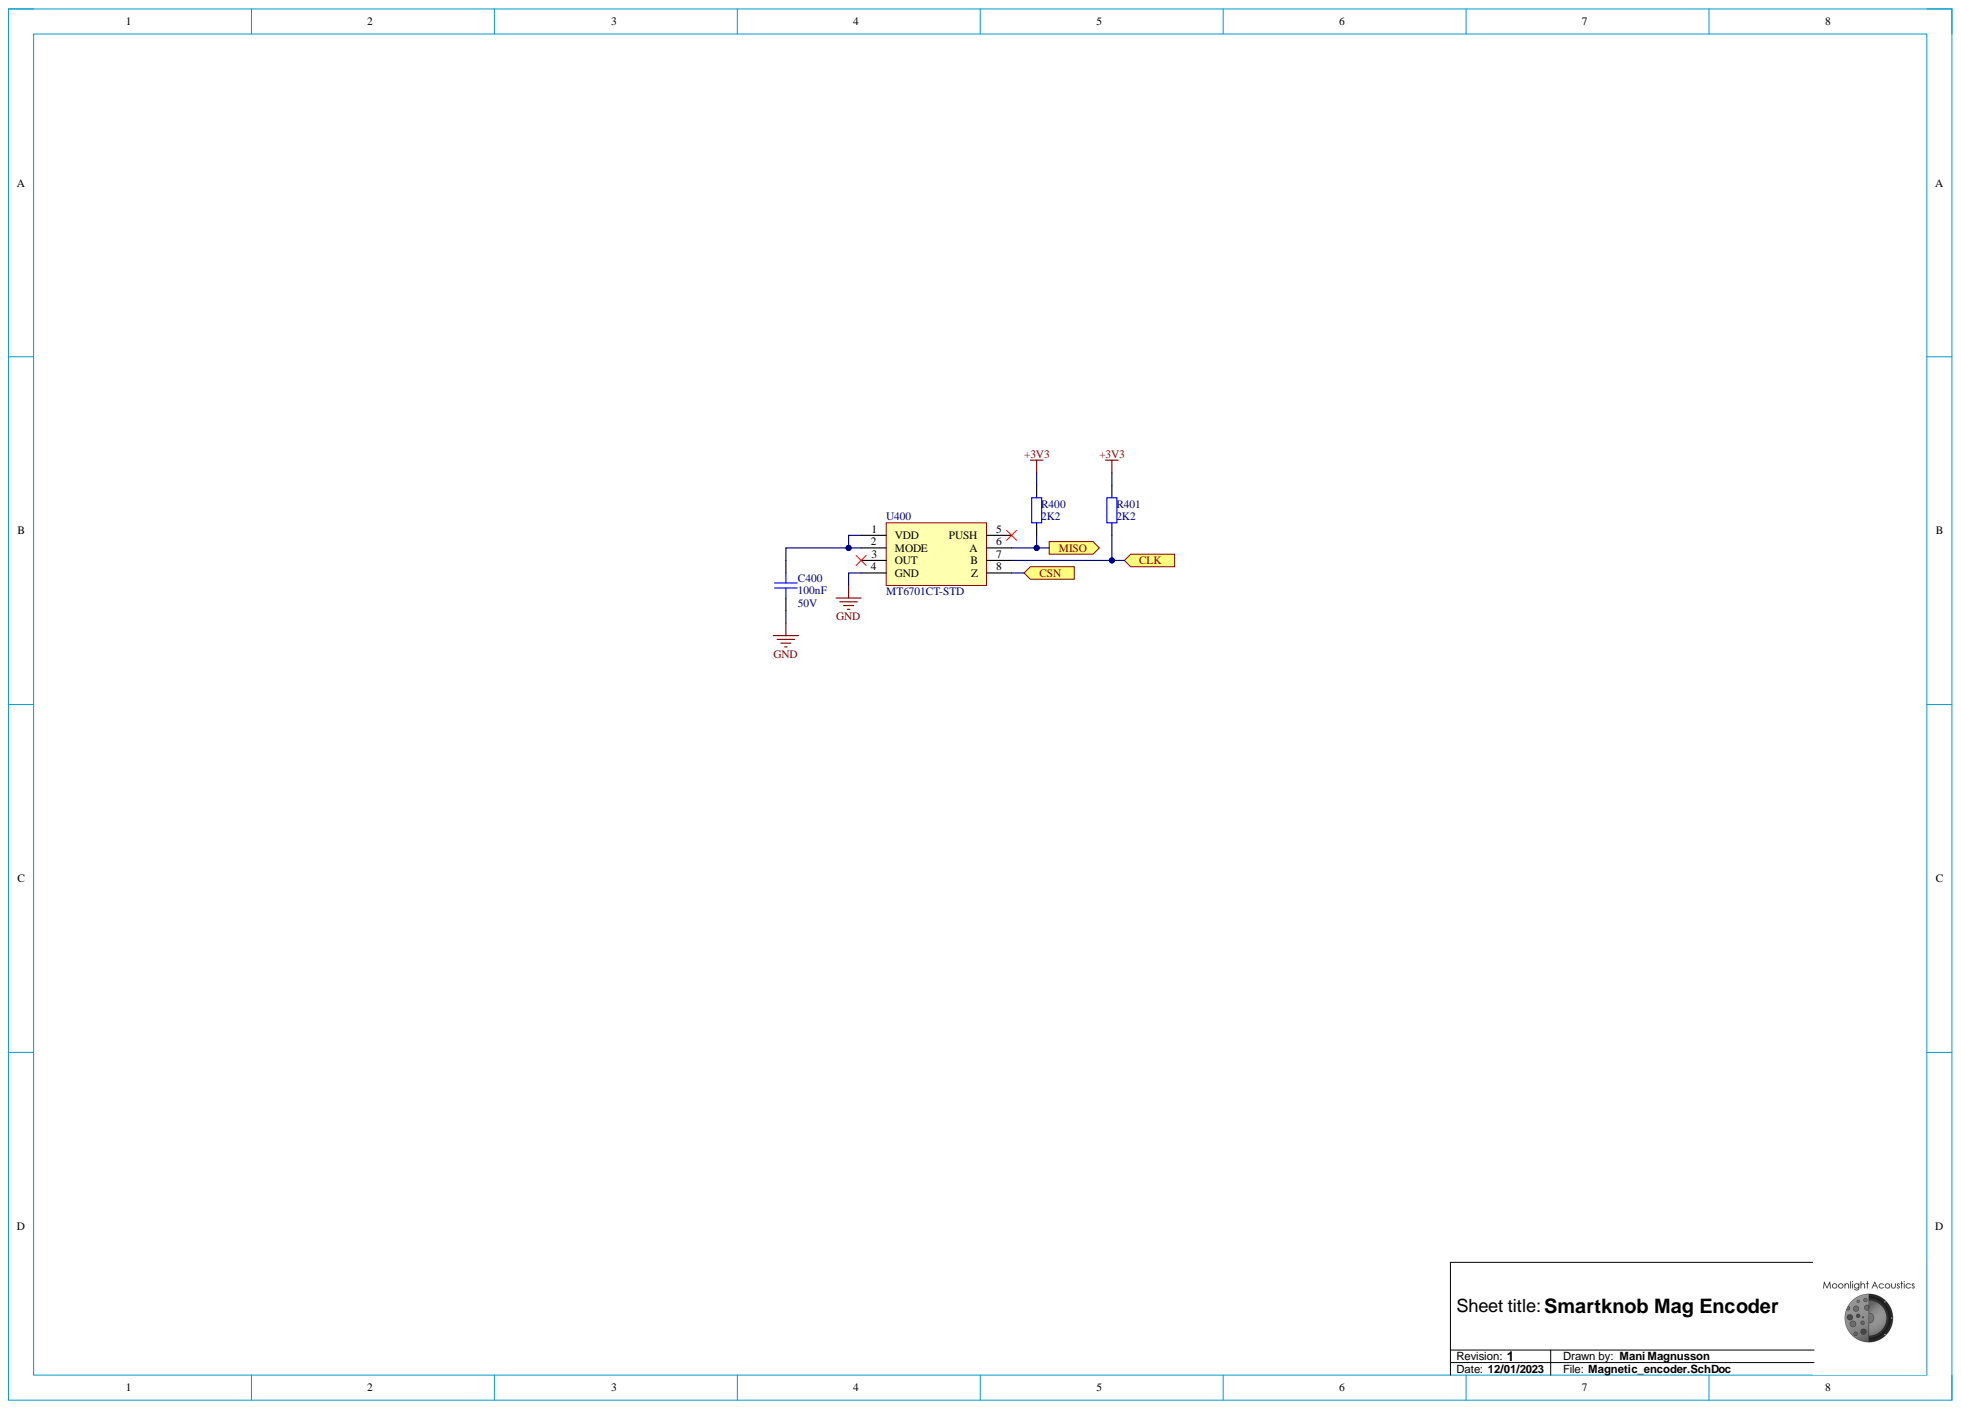
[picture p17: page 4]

Sheet title: Date: Revision:

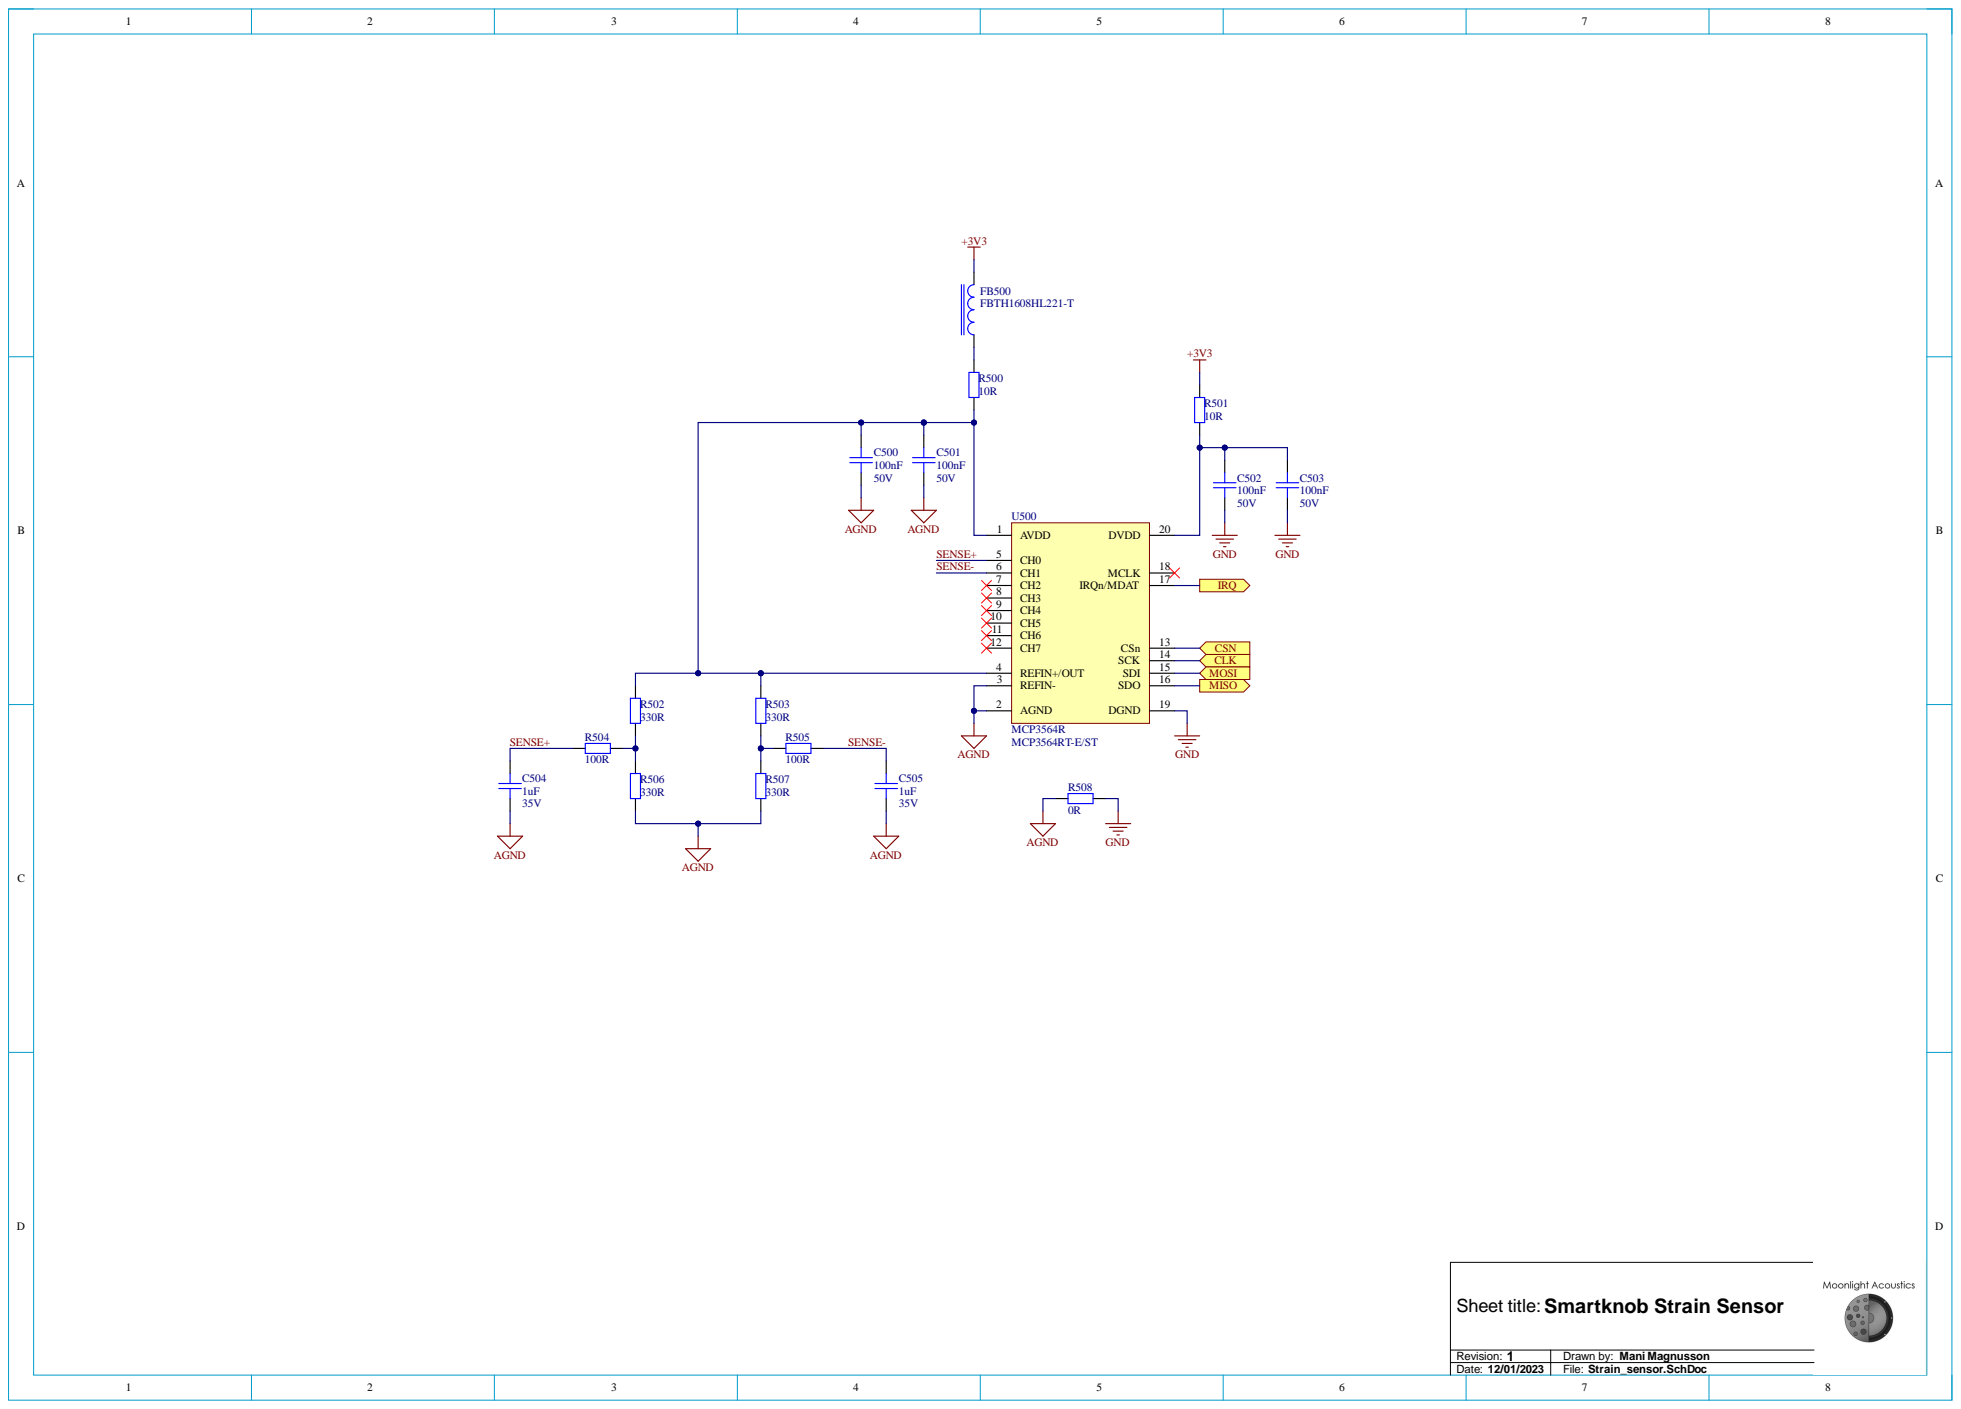
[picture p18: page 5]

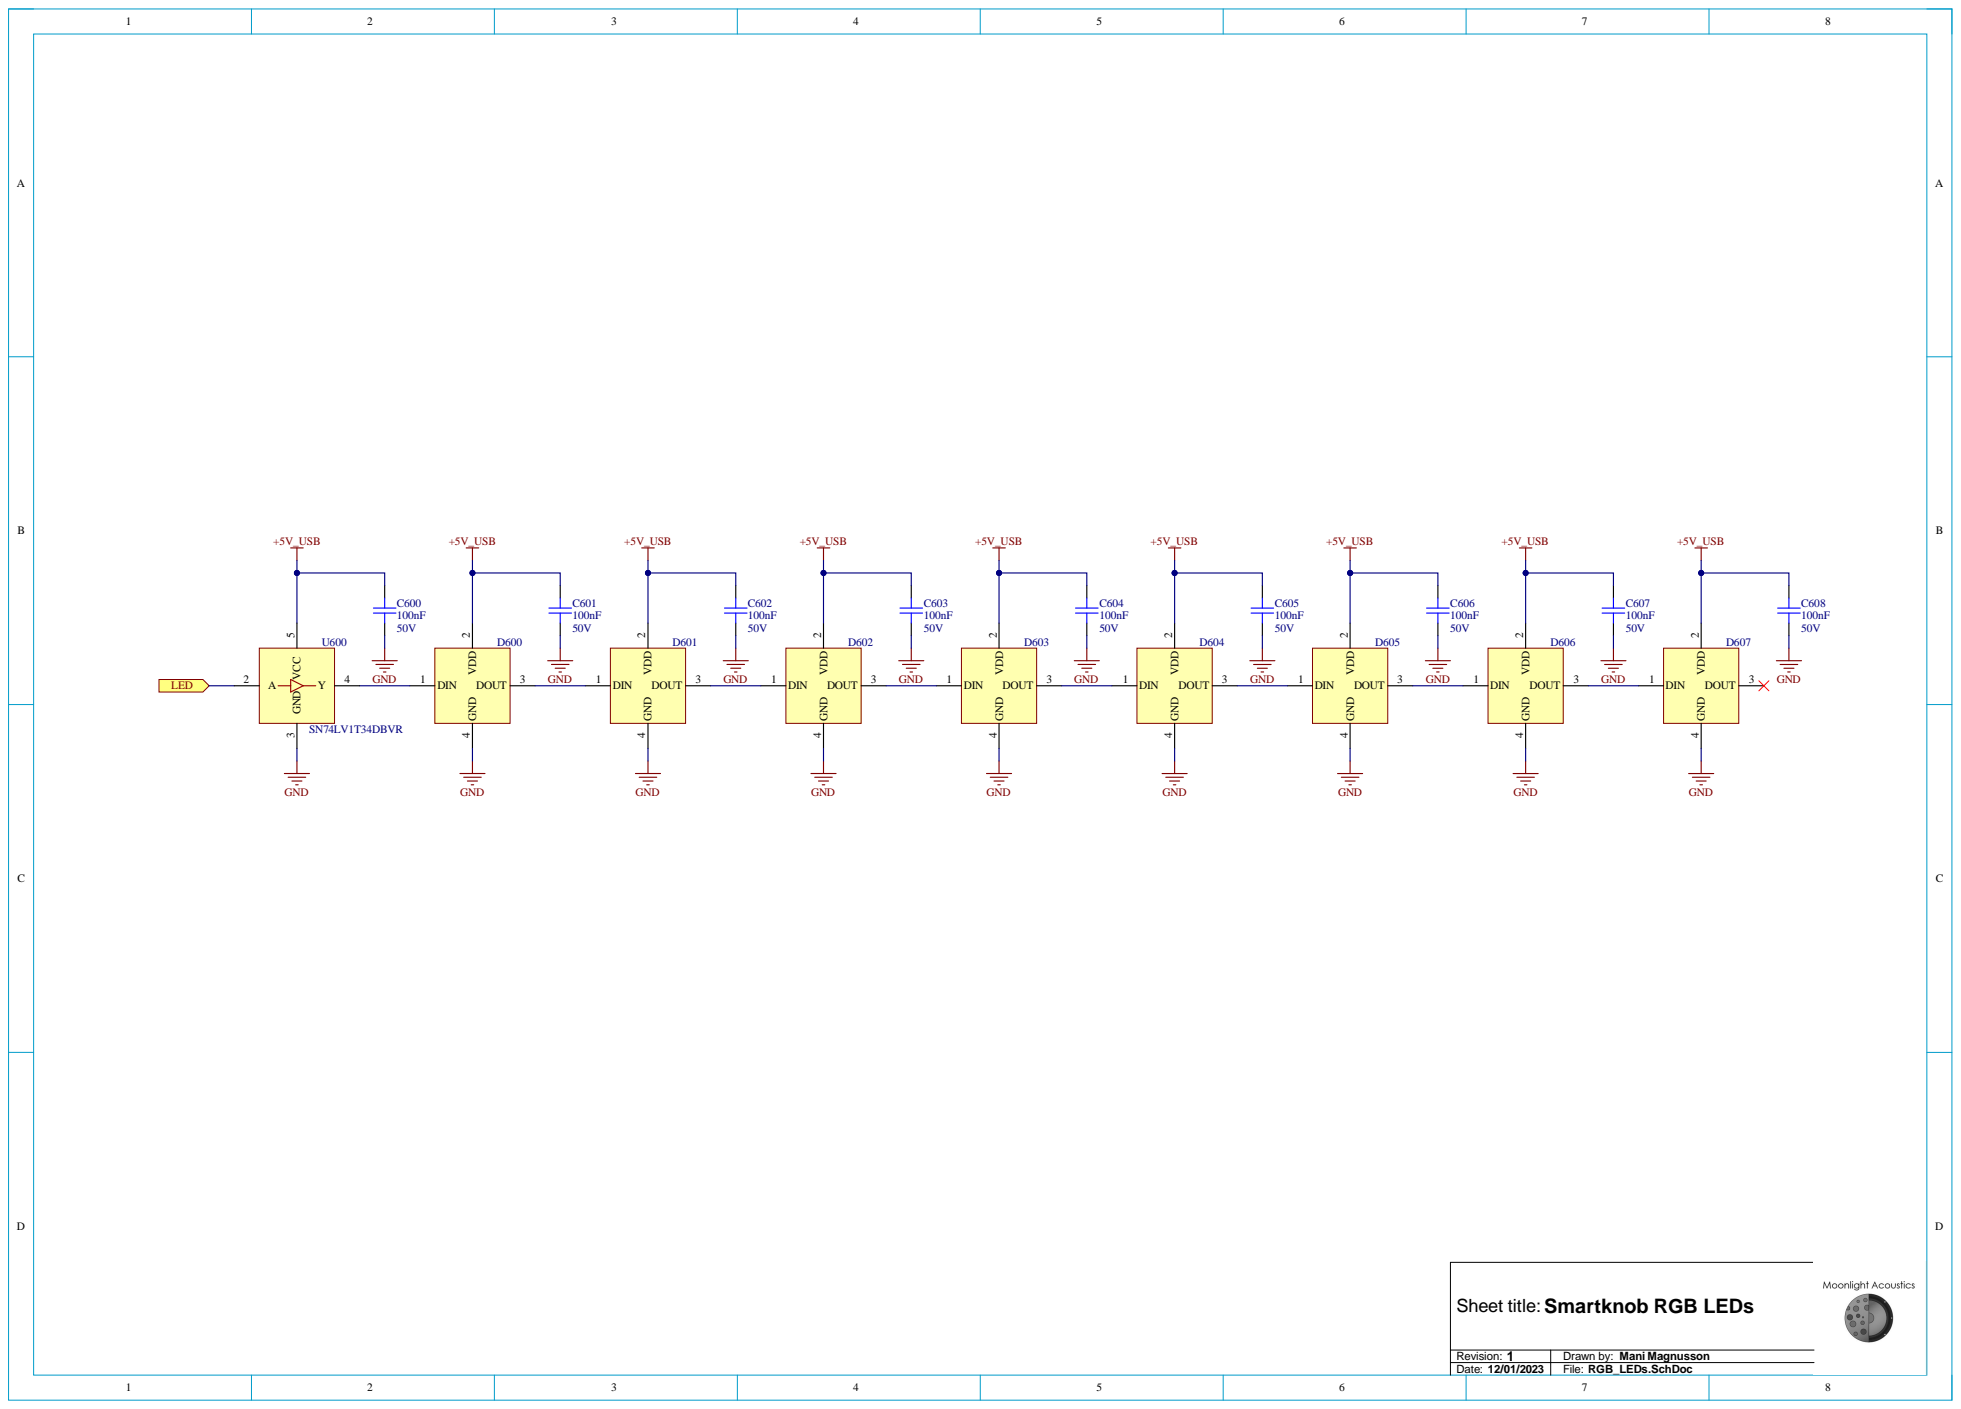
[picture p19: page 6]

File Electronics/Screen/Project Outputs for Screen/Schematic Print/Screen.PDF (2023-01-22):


LEDK 2 LEDA 3 VDD 4

GND 6 GND 5

GND 12

Drawn by: Mani Magnusson
File: Main.SchDoc

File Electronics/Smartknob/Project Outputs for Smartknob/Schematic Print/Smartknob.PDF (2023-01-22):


Drawn by: Mani Magnusson
File: Main.SchDoc


Place as close as
possible to pin 45

QSPI_SS | | | D- 8


1 0

Sheet title: Date: Revision:


Sheet title: Date: Revision:



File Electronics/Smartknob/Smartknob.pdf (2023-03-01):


Drawn by: Mani Magnusson
File: Main.SchDoc


Place as close as
possible to pin 45


VH 4
WH 5
UL 6
VL 10
WL 7

+3V3 | DIAG 12 VIO/nSTDBY 11


Sheet title: Date: Revision:









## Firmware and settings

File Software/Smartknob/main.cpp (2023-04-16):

/*
 *  Title: Smartknob

 *  Description:
 *      Read data from SCD30 via i2c and print over USB serial
 *      REPLACE WITH ACTUAL DESCRIPTION
 * 
 *  Author: Mani Magnusson
 */

#include <string.h>
#include <math.h>
#include <stdio.h>
#include <pico/stdlib.h>
#include <pico/time.h>
#include <hardware/spi.h>
#include <MT6701.h>
#include <MCP3564R.h>
#include <FOC.h>
#include <TMC6300.h>
#include <PID.h>
#include "pin_assignments.h"

// Defines & constants
const float _pi = 3.14159265358f;
const float _3pi = 9.42477796076f;
const float _2pi = 6.28318530717f;

// Constructors
MT6701 mt6701(spi1, MAG_CSN);
MCP3564R mcp3564r(spi1, STRAIN_CSN);
TMC6300 tmc6300(UH, VH, WH, UL, VL, WL, 5.0f);
FOC foc(7, &mt6701, &tmc6300, Direction::CCW, 5.0f);
SMARTKNOB::PID knob_pid(8.0f, 0.0f, 0.02f, 10.0f);

// Variables and data structures
struct Config {
    bool coarse = true;
    bool smooth = false;
    int32_t position = 0;
    int32_t min_position = INT32_MIN;
    int32_t max_position = INT32_MAX;
    float detent_center = 0.0f;
    float snap_radians_decrease = -_pi / 16.0f;
    float snap_radians_increase = _pi / 16.0f;
    float torque_limit = 2.5f;
} config;

struct repeating_timer timer;
float angle = 0.0f;
uint8_t channel = 0;
int32_t measurement = 0;

// Forward declarations
bool repeating_timer_callback(struct repeating_timer* t); // Interrupt timer callback

template <typename T> T constrain(T amt, T low, T high) {
    if(amt < low) return low;
    if(amt > high) return high;
    return amt;
}

void init() {
    stdio_init_all();
    sleep_ms(100);
    spi_init(spi1, 10000000u);
    spi_set_format(spi1, 8, spi_cpol_t::SPI_CPOL_0, spi_cpha_t::SPI_CPHA_0, spi_order_t::SPI_MSB_FIRST);

    // Initialize GPIO
    gpio_set_function(MAG_MISO, GPIO_FUNC_SPI);
    gpio_set_function(MAG_CLK, GPIO_FUNC_SPI);
    //gpio_set_function(STRAIN_CLK, GPIO_FUNC_SPI);
    //gpio_set_function(STRAIN_MISO, GPIO_FUNC_SPI);
    //gpio_set_function(STRAIN_MOSI, GPIO_FUNC_SPI);
    //gpio_init(STRAIN_IRQ);
    //gpio_set_dir(STRAIN_IRQ, GPIO_IN);
    //gpio_pull_up(STRAIN_IRQ); // Required for MCP3564R to work!

    // Init MT6701
    mt6701.init();

    // Init TMC6300
    tmc6300.init(24000L, 0.05);
    tmc6300.set_enabled(true);

    // Init FOC
    foc.init(false, true); // Set to sine mode
    foc._zero_electric_angle = 4.062365f;
    printf("Zero Electric Angle: %f\n", foc._zero_electric_angle);

    // Init detents
    mt6701.read(&angle);
    config.detent_center = angle; 
    config.max_position = 50;
    config.min_position = 0;

    // Init MCP3564R
    /*
    mcp3564r.init();
    mcp3564r.set_clock_source(3);
    sleep_us(100);
    mcp3564r.select_vref_source(false);
    sleep_us(10);
    mcp3564r.set_data_format(3);
    sleep_us(10);
    mcp3564r.enable_scan_channel(8);
    sleep_us(10);
    mcp3564r.set_adc_gain(5);
    sleep_us(10);
    mcp3564r.set_oversample_ratio(6);
    sleep_us(10);
    mcp3564r.set_conv_mode(3);
    sleep_us(10);
    mcp3564r.set_adc_mode(3);
    sleep_us(100);
    printf("Finished initializing.\n\n");
    */

   // Init PID
   knob_pid.errorMode = SMARTKNOB::ErrorMode::ANGULAR;
   knob_pid.derivativeMode = SMARTKNOB::DerivativeMode::DERIVATIVE_ON_ERROR_FILTERED;
   knob_pid.setpoint = angle;

   // Add an interrupt timer
    add_repeating_timer_us(-1000, repeating_timer_callback, NULL, &timer);
}

void loop() {
    //mcp3564r.read_data(&measurement, &channel);
    //printf("ADC data: %d\n", measurement);
}

bool repeating_timer_callback(struct repeating_timer* t) {
    mt6701.read(&angle);
    knob_pid.setpoint = config.detent_center;
    float torque = knob_pid.update(-angle, 0.001f); // Set dt to 1 ms since this loop is interrupt based
    foc.update(constrain(torque, -config.torque_limit, config.torque_limit), &angle);
    if((knob_pid.error > config.snap_radians_increase) && (config.position > config.min_position)){
        config.detent_center = fmodf(config.detent_center - 2.0f * config.snap_radians_increase + _3pi, _2pi) - _pi;
        config.position--;
        printf("Gain: %d dB\n", config.position);
    }
    if((knob_pid.error < config.snap_radians_decrease) && (config.position < config.max_position)){
        config.detent_center = fmodf(config.detent_center - 2.0f * config.snap_radians_decrease + _3pi, _2pi) - _pi;
        config.position++;
        printf("Gain: %d dB\n", config.position);
    }
    //printf("%f\n", angle);
    return true;
}

int main() {
    init();
    while(1) {
        loop();
    }
    return 0;
}

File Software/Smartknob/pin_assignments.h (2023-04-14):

#pragma once

// LCD pinout
#define LCD_DC 0
#define LCD_CS 1
#define LCD_CLK 2 // SPI 0 SCK
#define LCD_MOSI 3 // SPI 0 MOSI
#define LCD_RST 4
#define LCD_BL 5

// RGB LED pinout
#define LED 6

// Strain sensor pinout
#define STRAIN_IRQ 7
#define STRAIN_MISO 8 // SPI 1 MISO
#define STRAIN_CSN 9
#define STRAIN_CLK 10 // SPI 1 SCK
#define STRAIN_MOSI 11

// Motor pinout
#define WH 12
#define WL 13
#define VH 14
#define VL 15
#define UH 16
#define UL 17
#define DIAG 18

// Magnetometer pinout
#define MAG_MISO 24 // SPI 1 MISO
#define MAG_CSN 25
#define MAG_CLK 26 // SPI 1 SCK - MAX 15 MHz

// General GPIO/UART/I2C pinout
#define GPIO_1 28
#define GPIO_2 29

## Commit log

2022-11-01 Started adding microcontroller section
    [Main.SchDoc, Microcontroller.SchDoc, Smartknob.PrjPcb]
2022-12-18 Add schematics
    [Magnetic_encoder.SchDoc, Main.SchDoc, Microcontroller.SchDoc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]
2022-12-23 Finish schematic for base
    [Main.SchDoc, Microcontroller.SchDoc, RGB_LEDs.SchDoc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]
2023-01-11 Start PCB layout
    [Magnetic_encoder.SchDoc, Main.SchDoc, Microcontroller.SchDoc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]
2023-01-14 Create screen project, begin main board layout
    [Main.SchDoc, Screen.PcbDoc, Screen.PrjPcb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]
2023-01-15 Continue component placement
    [Motor_driver.SchDoc, Smartknob.PcbDoc, Strain_sensor.SchDoc]
2023-01-22 Continue layout
    [Smartknob.PcbDoc]
2023-01-22 Continued layout
    [Bill of Materials-Screen.xlsx, Bill of Materials-Smartknob.xlsx, Main.SchDoc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]
2023-01-23 Start routing
    [Smartknob.PcbDoc]
2023-03-01 Just finish the whole thing
    [Bill of Materials-Smartknob.xlsx, Magnetic_encoder.SchDoc, Main.SchDoc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]
2023-03-13 Fix mechanical issues
    [Screen.PcbDoc, Screen.step]
2023-03-16 Add software
    [BaseMount.stl, Baseplate.stl, Enclosure.stl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]
2023-03-24 Minor main PCB changes
2023-04-03 Change pico-sdk to develop branch
2023-04-06 Fix MCP3564R issues and document it in readme
    [main.cpp]
2023-04-10 Add FIR filter library
2023-04-16 Fix FIR class, add PID and implement detents
    [main.cpp]
2023-04-16 Fix author credits in PID library
2026-03-19 Start updating to next version and add gitignore
    [Main.SchDoc, Microcontroller.SchDoc, RGB_LEDs.SchDoc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]
